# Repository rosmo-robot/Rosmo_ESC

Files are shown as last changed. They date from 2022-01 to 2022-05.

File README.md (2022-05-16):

# Rosmo ESC

Design for [Rosmo](https://rosmo.io) ESC - in M5Stack format.

[Schematic (PDF)](./Rosmo_ESC.pdf)

Top:
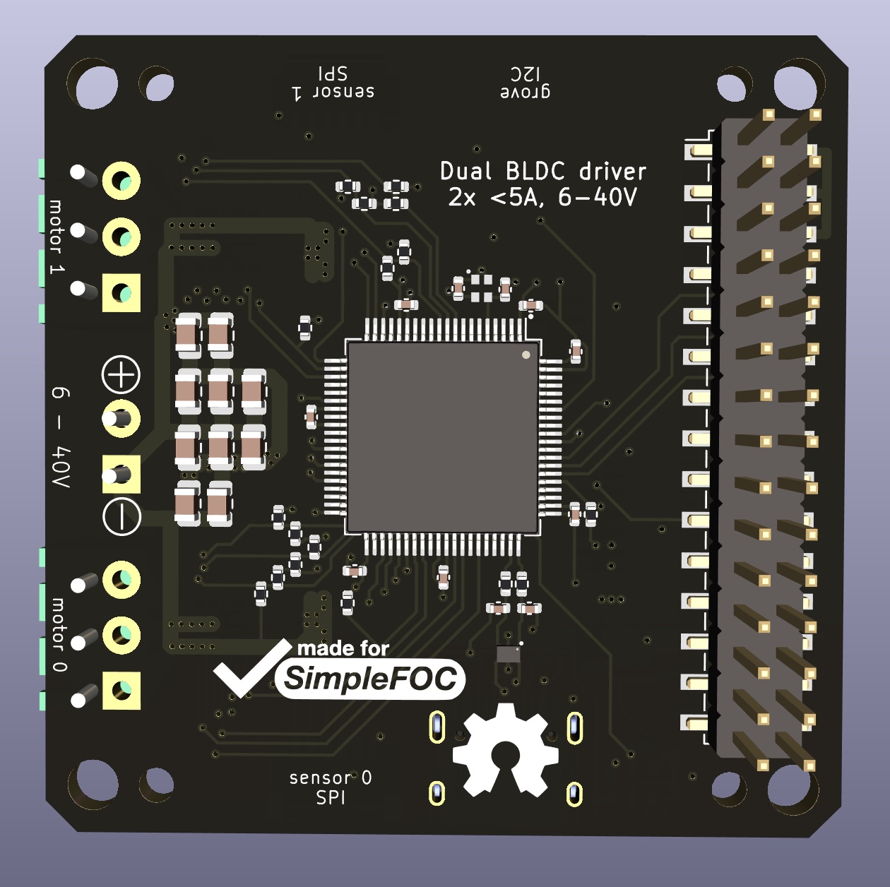
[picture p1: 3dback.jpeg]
3d render bottom 3D render of back

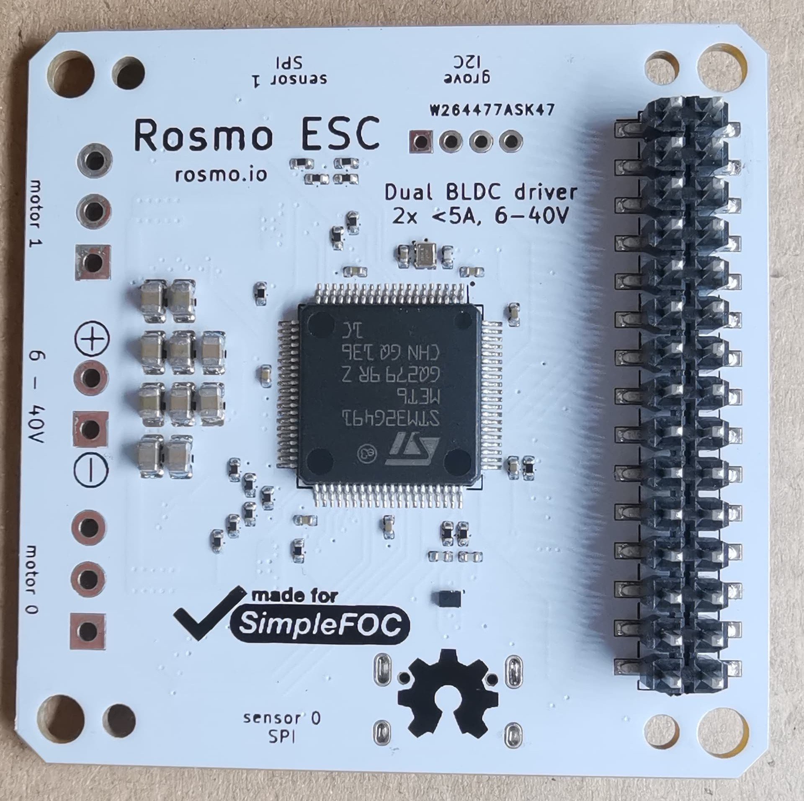
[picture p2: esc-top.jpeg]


Bottom:
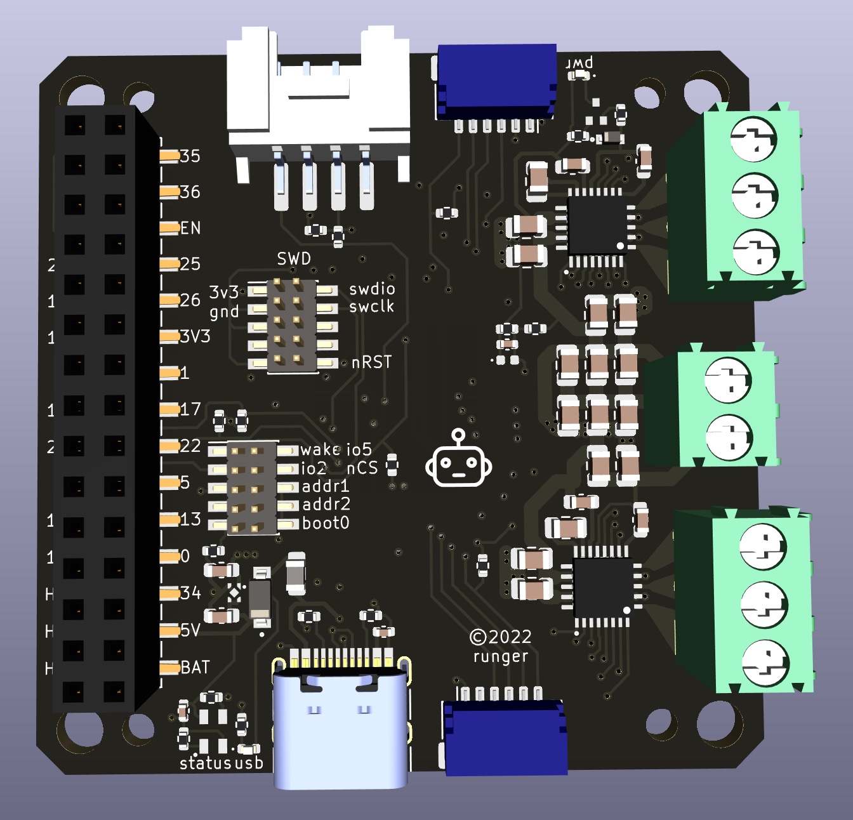
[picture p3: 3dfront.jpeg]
3d render top 3D render of top

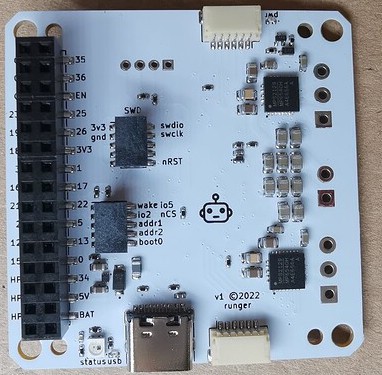
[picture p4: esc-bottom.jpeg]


## Features

* Dual brushless motor ESC in M5-Stack module format
* Drives 2x 3-phase BLDC motors with up to 40V and 5A (cooling needed - to be tested)
* 2x SPI sensors supported, such as MA732, MA730, AS5048A, AS5047, etc...
* Control inputs via SPI, I2C    (and GPIO:question:)
* Grove port for I2C input/output

## Status

:warning: In development, prototype boards on order.

At the moment, schematic is complete and board has been routed. The BOM is complete but my have to change due to component availability.

**Do not use this for anything yet!**

## Pinout

Prototype pinout, based on STM32G491MET6, which is probably not the final MCU for this design, but a suitable (if maybe overpowered and therefore expensive) one that was available in the current semiconductor shortage. This MCU is 12x12mm LQFP-80, which is more than enough pins.

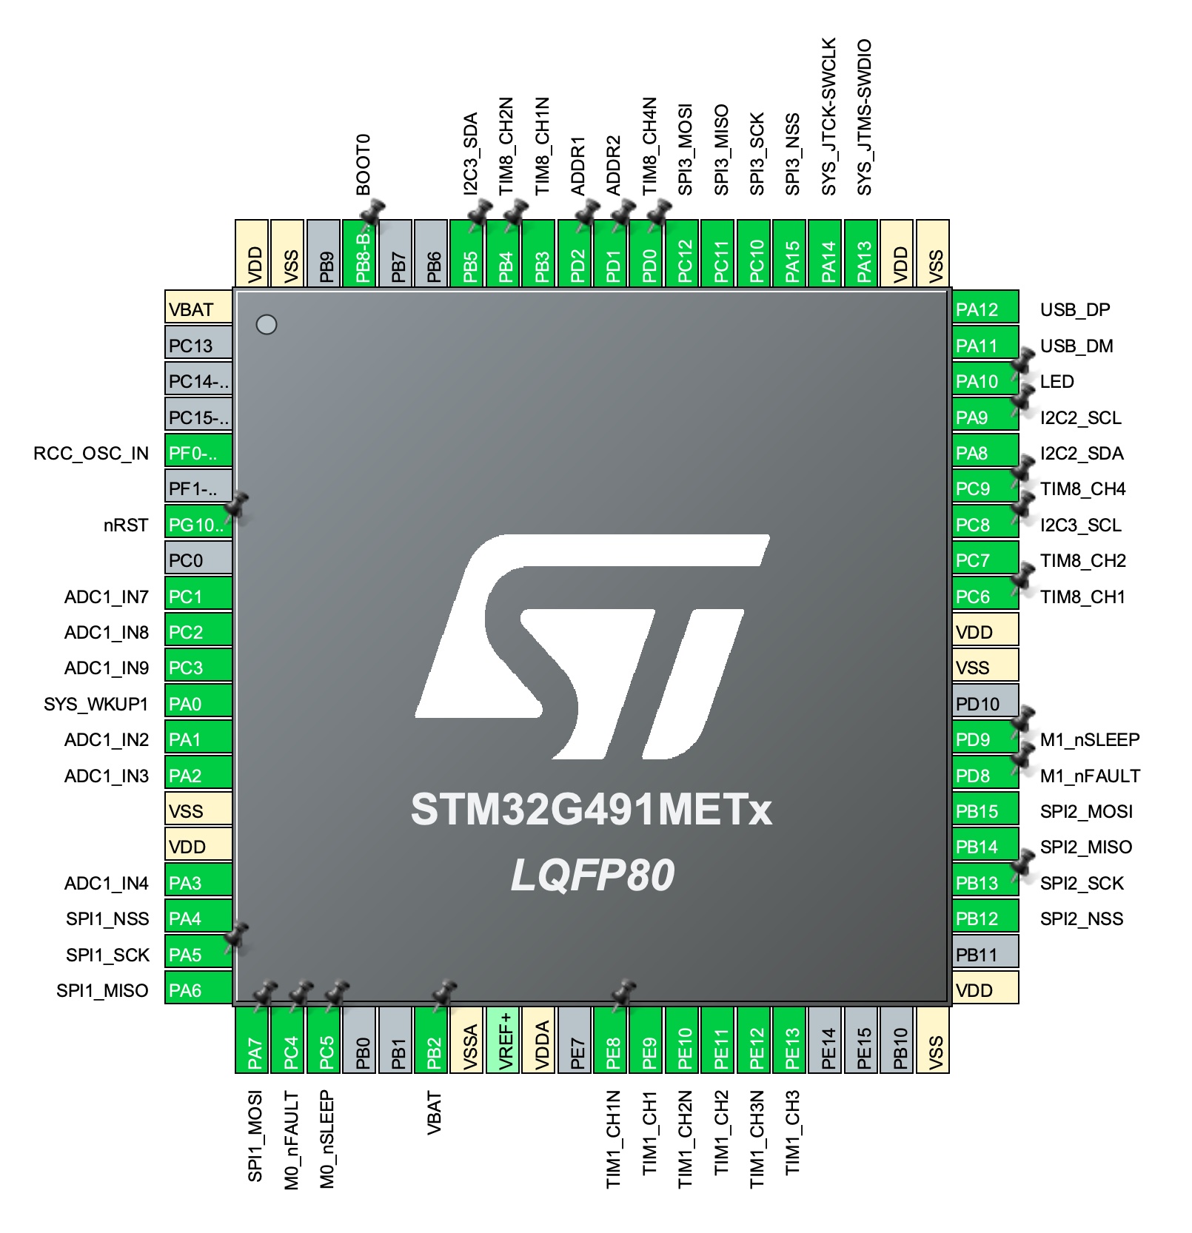
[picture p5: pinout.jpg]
pinout STM32G491MET pinout


Functionality supported by this pinout:

* 2x 3-phase BLDC motor control with 6 PWM (6 outputs on TIM1 and 6 on TIM8, in CHx/CHxN configuration)
* 2x nSLEEP outputs (GPIO)
* 2x nFAULT inputs (interrupt GPIO)
* 2x 3-phase low-side current sensing (6 single-ended inputs on ADC1)
* 1x battery voltage monitor (1 single-ended input on ADC2)
* 3x SPI w/ hardware NSS pin (2 sensor ports + M5 stack SPI pins)
* 2x I2C (grove port + M5 stack SPI)
* USB FS connected to USB-C port (should allow serial monitor function and DFU firmware flashing)
* WAKE input (M5 GPIO connected to system wake 1, so M5 ESP32 can wake STM32 from sleep)
* SWD debug pins connected to standard ARM-10 debug header
* LED pin connected to status LED (or NeoPixel LED)
* BOOT0, nRST, OSC_IN - STM32 system pins

## Dependencies

The design uses various custom symbols and footprints. They should load from the project-internal cache when you open the project. If they do not, you can find [a kicad library](https://github.com/runger1101001/kicad-lib-runger) here which contains all the symbols/footprints used, among others.

Uses KiCad 6.

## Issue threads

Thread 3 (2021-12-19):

Check clearance between screw terminals & M5 core

samuk, 2021-12-19:
We should check that the screw terminals have enough clearance when the M5 header is in place, stacked below an M5core or [Open Core ESP32](https://oshwlab.com/Rosmo/m5-proto)

runger1101001, 2021-12-19:
My plan is to use "pluggable terminal blocks" like the ODrive M5 module. I like that idea.

Normal terminal blocks won't work because the screws would not be accessible. And other connectors are either expensive, too bespoke, require crimping, etc, etc... the pluggable terminal blocks combine the ease of use and ubiquity of screw-connections with the "front access" only type of profile we need.

The pic here illustrates it nicely:
http://free-electronic.com/product/pluggable-terminal-block-2-pin/

So I have to find the ones we'll use (Amphenol I think, they're cheap) and I can send you the dimensions.

samuk, 2021-12-28:
Resolved

Closed 2021-12-28.

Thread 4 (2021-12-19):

Did you route the current outputs to mcu opamp capable pins?

samuk, 2021-12-19:
I noted you implemented the current sensors on each axis.

Did you route the current outputs to mcu opamp capable pins?

From Twitter: https://twitter.com/uuLipe/status/1472671409084243969

runger1101001, 2021-12-19:
Hmmm.. no I didn't pay attention to it. The driver has current sense amps built-in, so the signal is already amplified and in the right range for the ADC via the external resistors (if my calculations are correct!). What would the op-amps be used for?

uLipe, 2021-12-19:
Thanks for highlight my comment on twitter.

Sounds fair enough to me, I didn't noted the built-in amplification block on the driver.

samuk, 2021-12-19:
No worries, thanks for your interest. Would you be interested in testing the boards if we get a batch made?

uLipe, 2021-12-20:
@samuk , for sure, I also have m5 stack esp32 modules here and it would be great to write an initial microROS network using these modules being an initial skeleton of an mobile robot.

Closed 2021-12-19.

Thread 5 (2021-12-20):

Repository for the module firmware.

uLipe, 2021-12-20:
I think since the general idea of the hardware is up, the repository for the firmware as well the design discussions would be started.

I see this module as one of most exciting microROS over serial use cases, hot-pluggable to other microROS instances.

samuk, 2021-12-20:
Absolutely! There are a few notes in the [Rosmo doc](https://cloud.transition-space.org/apps/onlyoffice/s/KyTnsYjs4GRkXjZ), but worth discussing further.

Useful background is to know that @runger1101001 is the author of [I2C commander](https://github.com/simplefoc/Arduino-FOC-drivers/tree/master/src/comms/i2c#controller-device-brain-mcu). The ESC board will run this.

Beyond that I think it may fall into three phases;

1) A very simple [Bluetooth car](https://github.com/Yapele/Android-phone-accelerometer-controlled-Remote-Car) & I2C-commander to control to test the board(s) and bring the robot alive

2) Development of a block, or set of blocks for [Ottodiy](https://github.com/OttoDIY/blockly)which communicate using I2C-commander. I think we can probably do this in the medium term with our current capacity. Ottodiy has expressed some interest in this.

3) The uRos work. This is less clear at this point. It might involve developing this [diffdrive code](https://github.com/rosmo-robot/Rosmo_ROS2_Diffdrive) to have similar functionality to I2C-commander-master. It may make sense to use the ROS2 stack of https://nanosaur.ai/ as they seem open to collaboration, and it would save reinventing the wheel there. There is also interesting work happening in the #stackchan community around uROS, so we'll keep an eye on that. We need more people to get involved to make the uROS/2 work a reality.

runger1101001, 2021-12-20:
In terms of the firmware, we have to separate the different parts:

- the "module firmware" will target the STM32G4 MCU on the driver module. It will be expected to have a clean outward API towards the M5-stack's core MCU, probably via I2C. Th expectation is that the normal user will change this firmware rarely, if ever (so the final module may not have the USB port, to be discussed). This firmware will run SimpleFOC, which is an Arduino library. I see that µROS supports some Arduino hardware (though none with STM32G4 at the moment) - so I'm not sure how easy it is to marry these two things.
- the M5 core firmware, which talks to the motor drivers and handles all the higher lauer stuff. ESP32 is supported by µROS, and this is where I would see the freeRTOS based layer coming into play.
- the application software like blocky or a remote control app, which run on hardware external to the robot

For my part I would begin by creating a module firmware repo as the ticket suggests, based on Arduino framework, SimpleFOC and a fairly simple control layer, similar to the many commonly available I2C motor shields.

samuk, 2021-12-20:
I think we agree that the "module firmware" on the ESC driver board can always remain Arduino?

In an Otto/Blockly use case, the 'Brain ESP32' would run Arduino & I2C-Commander-Master and speak over I2C to the ESC device.

In a uROS use case the 'brain ESP32' may run Arduino (or it may be possible to port I2c-commander-master to FreeRTOS), it speaks to the ESC driver board over I2C. The 'brain ESP32' is also communicating with a Jetson/Pi/Coral over Wifi or Ethernet for the higher level ROS2 stuff.

uLipe, 2021-12-20:
I would like to add some points from the optics I have been seen when working with robots as a distributed system.

- Treat them as an isolate subsystem is great, implementing the firmware separately of the ESC on the foc module, and basic robotics stuff ( high level controllers + kinematics server) in the ESP32 sound really nice and reinforces the principle of single responsibility.

- I think the SRP design would be even greater if the modules foc, esp32 and other devices like future sensors could take advantage of same interface, allowing them to be plug-in-play, and visible across other subsystems in a form of topics.

- And here is where microROS comes into play, it would be possible to model the foc modules as abstract boxes that control motors and expose them in a format of topics, publishing commands and parameters and subscribe for their state. Same for the esp32, by modelling it as an robot brain with relevant topics.

- The microROS in their latest design support custom transports ( over UART, thus I2c), and more recently the embeddedRTPS making any microROS instance to be discoverable direclty from a full ROS2 system ( on a PC or SBC), the integration and expansion of this robot system would be smooth, since model it in abstract way, let micro ROS handle the distributed process and deal with subsystem specific role, brain, foc, imu, etc.

Would be interested in a rough draft of this design, I can spend some time on it and share with you.

Just to remember, microROS is compatible with both Arduino, and esp-idf, also it is supported from Nuttx and Zephyr which recently is being supported officially by espressif as platforms.

samuk, 2021-12-20:
`Would be interested in a rough draft of this design"`

Yes! That sounds interesting to me at least. @runger1101001 ?

As an aside, the guys at https://www.luos.io/ were quite interested in the Rosmo concept and might be interested in using the platform as a demo of Luos. Not sure how much time they actually have, or if that's just a further distraction for us in an already complex project.

runger1101001, 2021-12-20:
Yes, I would be very interested! I have to quickly add though that due to my lack of knowledge on µROS and time constraints I would support but not lead that development effort.

Regarding luos, that's also an interesting project! I'm discovering so many interesting things thanks to you, sam!

I will (as so often, sorry!) add a concern to the equation: when doing this distributed robotics/control stuff, and also when dealing with something like luos, you have to look at the real-time requirements of the components and put everything in the right place, or it just won't work.
What do I mean? For example, the FOC control of the motors is highly real-time, sub-millisecond. To run either the FOC-loop or the move-loop remotely from the PWM generating MCU is not feasible.
The next level, motion control, i.e. coordinating 2 or more motors to achieve a desired trajectory for a robot - it may be possible to run that on a remote MCU. It will be a tradeoff - comms latency will cause less responsive control and/or inaccuracy depending on the control method. Same goes for detecting and avoiding obstacles.
Higher levels like mapping and navigation are less real-time and can clearly be more easily distributed.

So despite the promise of their marketing, using a system like luos still requires a careful design of the overall architecture and what happens where, at least for a robotics system.

uLipe, 2021-12-21:
@runger1101001 that is true and I agree with you all concerns, when I worked in robotics company years ago, mostly of our final solution was a in-house engineering because at end of day the real-time requirements for having a multiple joint with high of DoF at the precise point are the main target to be achieved, so split high-rate control loops to run into bare-metal microcontollers to deal with servo controller.

At higher layer, and on the top of and ethercat bus, an single-board computer running realtime capable Linux dealt with waypoints and motion-planning + kinematics server in single ms timestep, and was responsible to generate all joints commands (position, velocity, torque).
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
uLipe, 2022-01-03:
Yes, I thinks both can coexist, the point of openning the FoC states for the host is to provide a huge advancement to the ESCs out there, which is the flexibillity of control the commands and states which the only ESC that provides that is Odrive, which would be a pain to build from source.

uLipe, 2022-01-10:
@samuk , @runger1101001 , should I start to port the I2C commander as a esp-idf component?

samuk, 2022-01-10:
@uLipe I'm excited at the prospect. The principle sounds good. I defer to @runger1101001 on the timing question.

runger1101001, 2022-01-10:
Hey, if you want to start, I definately don't want to stop you!!

I am planning some refactoring of the I2CCommander, but this will be mostly on the receiving side. In the longer term future I would like to add SPICommander and CANCommander, using the same registers, and might refactor a little more at that point.

The I2C master is really very simple, you could port what is there with not much effort. The important part is really only the registers header file, which will give you the list of registers (commands) supported.
The rest of the I2CMaster is just send some bytes receive some bytes code, and could be solved in many ways.
Its important to carefully read/write always the right amount of bytes, or the I2C bus can become stuck.

A feature worth supporting is the "report" feature, which allows the master to define a set of registers as a "report", and then read all the registers with one command. That saves a lot of protocol overhead if you're always reading the same set of values, a common use case I would expect.

samuk, 2022-01-24:
@uLipe do you think you need any further info? Or would this be enough to get started?

uLipe, 2022-01-25:
Hello @samuk , @runger1101001 , sorry for being away these days, I got the flu.

I think from my side we have now sufficient information to start building firmware, said this would you folks think I can create the firmware repository for the motor controller?

Since its responsibillity is well defined, it is also simple to prorotype some circuits while the boards get ready.

If you give me the go, I will proceed creating the firmware repo, onde point, ArduinoFoC was engineered with Arduino in mind, so the motion controllers would be developed using the Arduino (Platformio?) ecosystem right?

uLipe, 2022-01-25:
Before I forget, have you chose a particular BLDC motor plus encoder? ArduinoFoC does not have the sensorless FoC (which I personally think is only usable in aerial robotics), se we need to define also the rotor position sensor. Of course I would always prefer an opto encoder with quadrature outputs.  Because SPI / I2C encoders are very slow to process in high speed scenarios or high velocity rate variation.

samuk, 2022-01-25:
@uLipe sorry to hear you've been ill. Welcome back.

Feel free to go ahead and create a repo. Yes SimpleFOC is an Arduino program. The I2C commander linked above will be the interface to it.

We're going to use these [magnetic encoders](https://github.com/rosmo-robot/Magnetic_Encoders/tree/master/Encoder_SPI#readme) that @runger1101001 has developed. As no one was selling them with SPI cabling/sockets he's just getting ready to produce & sell them on his Tindie page.

runger1101001, 2022-01-26:
Hey, when we're talking about the module firmware here, we're talking the ESP32 code... so the business of porting I2CCommanderMaster and doing the ROS integration...
For the ESC's STM32 firmware, I will make a repo, I have most of the code I need for that together already.

runger1101001, 2022-01-26:
And note there is no rush, the ESC boards won't be here until end of Feb, due to Chinese New Years.

uLipe, 2022-01-26:
@runger1101001 , thanks for clarification, I misunderstood the question.

That is said, I'm focusing on esp32 side, hopefully I have an m5stack core in my hands so I can consider they form factor to bring-up the component.

By moving with the IDF approach, the module firmware would be a component compatible to the ESP-IDF and inside it it would be possible to provide some application through an example folder, which is compliant with IDF component structure.

Other thing I would like to highlight is uROS supports WIFI interface, which I see very interesing cases of Rosmo robot fleets :)

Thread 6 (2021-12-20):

Support for CAN-Bus

uLipe, 2021-12-20:
I see the module uses an overpowered stm32 microcontroller.

Since this is true, what about select a cheaper one like stm32g431, which has CAN and leave this possiblity besides the traditional serial buses, making this module networkable :)

samuk, 2021-12-20:
@runger1101001 may have comment here.

Don't forget the existing modules which can be plugged in to add functionality. https://shop.m5stack.com/products/commu-module?variant=16804786896986

runger1101001, 2021-12-20:
Hey, this is a very good comment.

Yes, the MCU is somewhat overpowered. And it is expensive. And it is big. But, we were trying to create a prototype quickly, and it was available right now (only 20pieces) and so I ordered it and have it.

The final design should be optimised to use a different MCU if possible.

But, on the other hand, I would also make the following points:

- having more pins available than strictly necessary greatly eases both enabling the functionality (for example I think I could still activate CAN-bus, pins are available I think) and the routing, since pins can be moved around the MCU to find the best spot
- so a smaller 80 or 100 pin MCU would be appropriate
- LQFP is big, but in the end I routed it with only 0.6/0.3 vias - switching to a smaller MCU with 80 or 100 pins would mean BGA, and probably microvias, maybe even 6 layers, and ultimately a more expensive board
- driving 2 motors with 6-pwm and current sensing requires quite a bit of MCU power, so a G4 is actually not too overpowered

In terms of functionality:

- adding CAN would definately be possible, but unlike the grove I2C port which comes at the price of the connector + 2 pull-up resistors, a CAN bus would need a transceiver IC, 5V power, choke/filter, termination selection, etc... and I can tell you right now the small size CAN transceivers are all out of stock; since the CAN-bus can be added using existing M5-stack modules, we made the design decision to leave it off
- personally, I would add a buck converter to the design. Since we already have high voltage coming in, we could power the M5-stack from the ESC board, and save the user having to buy a separate base module for this
- the current design is "networkable" via I2C bus. We could easily add SPI to this, the design already connects to the M5 stack SPI bus, we would only need to add some headers to make the CS-pins selectable to enable multiple modules via SPI.
- CAN only makes sense if the modules are far apart. I'm not speaking out against CAN here, I think it is ultimately better than I2C, but also more expensive. In the context of M5-Stack, doesn't it make more sense to have stacks of drivers, locally connected via the M5-header to a M5 Core, which talks to them via I2C. The M5 cores have WLAN, and can communicate with each other that way. I think this approach is probably more what M5-users would expect?

uLipe, 2021-12-20:
All the comments above are reasonable, my point is to see the CAN-Bus as an additional, not a replacement from I2C or SPI.

The main point of CAN is the possibility to have an distributed network with bitrate higher than I2C, would be an option to route the CAN-TX + RX pins to solder pads and advanced users could stack an transceiver board if they have, I think would have some value to make this board "hackable".

The SPI option is great since it would allow to plug the m5 wiznet modules, allowing to make a true networkable, high-speed and maybe a microROS native motion module.

runger1101001, 2021-12-20:
Ok, I checked the pins, and the CAN is currently blocked by BOOT0, which I haven't routed out anywhere though. I'm unsure if it is needed - normally not for either DFU or SWD programming... perhaps a question for the STM forums to be sure, I can't 100% say from the datasheet. There are also BOOT-bits that can be set via the flags, so that could be another option.

Otherwise if BOOT0 is needed it could be used in conjunction with a CAN transceiver that has an EN-pin. Then we could disable CAN until boot-up is completed, and the BOOT0 pin would not be in the way. I'll try to see what can be done here.

The pins for a 2-pin (no flow control) USART connection are available though, so I will route those out still, and then we will have the option of asynchronous serial or RS485 as well.

samuk, 2022-01-07:
I think this is a wontfix for now so closing.

Closed 2022-01-07.

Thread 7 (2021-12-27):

Rosmo power supply concept?

runger1101001, 2021-12-27:
The power supply concept for Rosmo needs more attention.

The motors chosen are for 12V. They will run with less, but since they have quite high resistance the current, and hence the torque will be low.
m5stack power concept is very unclear to me. I can't find good documentation. [The schematic I can find ](https://github.com/m5stack/M5-Schematic/blob/master/Core/Basic/M5-Core-Schematic(20171206).pdf)has part of the power circuitry labeled "Speaker" :-( .

The general idea with m5stack seems to be that the core provides power to the rest, it has a 5V buck/boost converter with battery charging and 3.3V rails. It has a HPWR rail on the M5 header but it doesn't seem to connect to the core. The buck/boost converter is powered by the battery and the 5V_USB rail, and I assume will manage switching between these.

Currently the Rosmo ESCs 5V_USB rail connects into the 5V rail of the M5 header via a protective diode, so powering the core *should* would providing the Buck/Boost module doesn't mind this configuration (having its output back-powered).

An alternative could be to connect the 5V_USB to the VBAT on the m5 header, i.e. pretending to be a battery. Not sure if the buck/boost module will like that one either.

In any case the input to the ESC board should be at least 6V. The current design is for 4x1.5V battery, so this is just enough, but only when they're more or less charged up. Once they become empty the voltage would drop below 6V which is not ideal.

Note that the m5 core's battery charging is for 4.2V lipos or Lions, not for NiMH batteries in 4S. So I currently don't see how the m5stack itself is powered. The little battery in the base of the core module? – but the 3D design doesn't account for that...

Some ideas:

- get rid of the NiMH batteries in favour of a beefy 1S battery [like this](https://www.spystore.at/3-7v-2000mah-wiederaufladbarer-lithium-akku-e126849.htm) for example. This would get charged by the m5 core when plugged into USB, and could power everything for a little while. You'd need a boost converter board to boost it up to 12V for the ESC board input.
- use a 3S battery, something [like this](https://batteryzone.de/products/11-1v-2500mah-3s-hochleistungs-lithium-polymer-akku-fur-ferngesteuertes-auto-flugzeug-hubschrauber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). There are other shapes and sizes. The 11.1V will be fine for the ESC and motor. Use a buck converter module to produce the 5V to power the m5 stack.
- use the NiMH battery pack, together with a boost module to get 12V and a buck/boost module to get stable 5V.
- I'm sure there is a M5stack LiPo Power-Base? Integrate that into the design and use a 3S battery?
- Add a 5V buck converter to the ESC board. Then the ESC board can power the m5 stack directly from its 6V-40V input.
- Add both a 5V buck converter and 3.3V regulator to the ESC board: then the ESC is fully self-contained (i.e. could be used without the core module), and can power the m5stack if attached to it.

runger1101001, 2021-12-27:
Hmmm... this schematic for Core2 is a bit better: https://m5stack.oss-cn-shenzhen.aliyuncs.com/resource/docs/schematic/Core/CORE2_V1.0_SCH.pdf

It shows clearly that HPWR isn't connected to the core. The other issues around VBAT 5V_BUS are the same.

samuk, 2021-12-27:
Just to clarify my current thinking is to use 3x 3.2v lifepo4 cells: https://m.aliexpress.com/item/1005002959027031.html

They share the same physical dimensions as Aa batteries.

runger1101001, 2021-12-28:
Ok, I will try to find space for it! I'm more optimistic about that than the CAN bus TBH. I can't really fit another port around the outside.

samuk, 2021-12-28:
On board canbus would be nice, but would also add cost. Don't we get similar functionality from plugging in a M5comm module for those use cases that need it?

runger1101001, 2022-01-07:
Ok, I've spent about 10h on the buck converter and I'm changing my mind on this:

- due to chip shortage none of the designs I've made before can be produced at the moment
- designing a new one based on available chips is a bit of work, and carries some risk - risk that it won't be right and messes up the rest of the board. Then we'd have to manually desolder stuff to be able to use the prototypes, I'd prefer to avoid that, really
- having it on a board with MCU and all the other stuff is also an expensive way to prototype the buck converter, which only needs a few components itself

So the new plan to is to release the board as it is, adding only a 3.3V regulator so it is self-sufficient when plugged into USB.
For the prototyping, we can use one of the many cheap and tiny buck regulator modules ("BECs") that are available on AliExpress or eBay. There will be space for it in the Rosmo body.
Then I can design a new buck converter for the Rosmo board v2, prototyping it separately, and then integrating it into the v2 design. At that point we'll also have a clearer idea what we want - maybe with battery charging? Or maybe more basic, just for the ESC board and seperating it from the whole complexity of the m5 power?

samuk, 2022-01-07:
Great, thanks for investigating! This sounds like a sensible way forward. I'm happy to spend a bit of time looking at existing open-source buck designs to see what we could make in the current chip situation.

Closing this, for now, we can create a new ticket when we want to look at this again.

runger1101001, 2022-01-07:
No, the regulator is still missing and the m5 header... I'll export it again today if I can, but certainly before I order it.

Closed 2022-01-07.

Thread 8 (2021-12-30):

Create step file of board to enable case design

samuk, 2021-12-30:
@runger1101001 when you have time could you export a .step file of the ESC please so we can design the 3D print case to fit.

Ref
https://github.com/rosmo-robot/Rosmo_3D/issues/2

runger1101001, 2022-01-03:
[Rosmo_ESC.step.zip](https://github.com/rosmo-robot/Rosmo_ESC/files/7804330/Rosmo_ESC.step.zip)

The STEP export only includes the ports and a few components, all the other components don't get exported... but this should give the outer dimensions, and the since the ports are on there... note the terminal blocks are not the right ones...

samuk, 2022-01-03:
Nice one, thanks. Should be OK for the case design.

Closed 2022-01-03.

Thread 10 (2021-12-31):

Specify dimensions of encoder board

samuk, 2021-12-31:
As discussed it makes sense to develop a small encoder board so that users can plug and play the encoders. It would be good if this encoder could be used in a variety of motors.

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

I suggest we stick broadly to the above dimensions, whilst noting that the [BGM220](http://www.dys.hk/product/BGM2208-70.html) has 16mm spacing for the screw holes, so two 'notches' in the left and right of the above dimensions would give compatibility?

There would be a 7mm wide, side entry [JST SHR-06-VS ](https://www.jst-mfg.com/product/detail_e.php?series=231) without flange specified for soldering to the SPI side. This would be positioned 'in reverse' with the cabling going over the encoder chip so that it could be used in a [2205](https://ae01.alicdn.com/kf/H5db205d3acb24197b1f93c58d5f370b9e.jpg)

runger1101001, 2022-01-03:
Here a picture and 3D render:

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

This is the pinout:

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

These are the dimensions:

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

runger1101001, 2022-01-03:
If we can work with these for the prototype, then I have bunch here. I can provide AS5048As or TLE5012Bs in this shape.

If we want a different shape, we'd have to have some made :-)

samuk, 2022-01-03:
Great! nice one..

samuk, 2022-05-07:
These are now available here: https://www.tindie.com/products/smallrobots/as5048a-encoder-board-for-robots-motor-control/

Closed 2022-01-03.

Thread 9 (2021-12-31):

Export BOM

samuk, 2021-12-31:
It would be good to get a BOM, even if provisional and subject to change. It will enable us to get some ballpark production quotes.

runger1101001, 2022-01-03:
[Rosmo_ESC.csv](https://github.com/rosmo-robot/Rosmo_ESC/files/7804442/Rosmo_ESC.csv)

This is the current BOM.
This is the more or less finished board, but without the buck converter... I'm still playing with the design for that.

runger1101001, 2022-01-03:
I still need the part numbers for the M5 bus connector, top and bottom...

samuk, 2022-01-03:
Does this help? https://shop.m5stack.com/products/2x15-pin-headers-socket I can ask them on Twitter..

samuk, 2022-01-03:
Looks like you could specify the 3mm Samtec one? https://community.m5stack.com/topic/1980/pin-header-and-sockets-part-numbers

samuk, 2022-01-07:
In light of https://github.com/rosmo-robot/Rosmo_ESC/issues/7#issuecomment-1007344152 I think the BOM is final-v1 at this point?

runger1101001, 2022-01-09:
Hmmm... the Samtec one is 1.27mm pitch but the M5 bus is 2.54mm pitch. So that's not the right one. I'm beginning to to like this m5 stack so much, using custom connectors is just a pain.
If the grove port turns out to be a problem to procure I will change it to be a Stemma/QT I2C port instead.

I'm just going to assume standard 2.54 pitch SMD headers will work, the footprint looks like they will. We can ignore the alignment holes, I think, 30 solder joints should be strong enough for a few plug in/out cycles.

runger1101001, 2022-01-09:
Ok, this is more of an issue than I anticipated. Their custom connectors are also lower profile than standard ones. The lowest profile ones I've found so far, at mouser, have 3.05 or 3.6mm pins, but the standoffs are also taller than the m5 stack ones.
So you would end up with about 7.5-8mm distance between the board and the end of the pins.

But worse than that, these headers cost EUR5,50 each (!).

The smallest reasonably priced header will come to EUR0.70, but result in a board to pin distance of about 10mm.

I'll see if I can find anything else, at digikey for example... what a pain.

samuk, 2022-01-09:
If all else fails we could just buy the official one and have them shipped to whoever is doing the boards? https://shop.m5stack.com/products/2x15-pin-headers-socket

runger1101001, 2022-01-09:
I've included headers that should work - both sides for about $6, ugh. We can account for the difference in height in the ESCs shell, it will be a little taller module than necessary, but that could be a good thing anyway to get the heat out...

samuk, 2022-01-09:
Did you see these @75cents/ pc? https://shop.m5stack.com/products/2x15-pin-headers-socket

runger1101001, 2022-01-09:
I did look at that, but then I'd have to order them from m5stack, pay shipping+tax, send them back to china, pay shipping+tax, and by that time they wouldn't be any cheaper. And it would take an extra 1-2 weeks. Unfortunately, the forum already said PCBWay won't order from m5stack. And probably they wouldn't accept them for assembly anyway, since they're not on tape&reel.

Plus I don't really trust what I'd be getting. The picture says 10x set, the title says "4 pieces" and the description says "Includes 1xheader 1xsocket"...

I've put in the order for quotation... its a little more than I anticipated, they won't give the $30 assembly deal for some reason, prob. because it has 102 components or something. So for 10 boards + assembly it will come to $300 or so + the components, which still have to be quoted, but I'm guessing will come in at another $400 (counting the drivers and MCUs which I already have at around $20).

So we're looking at somewhere around $70/board for a quantity of 10. Looking at the prices for making 50 pieces, it looks like the price would  be more like $10/board + components, so $30-$40/board.

runger1101001, 2022-01-09:
Yeah, its the component count that's driving up the price... but if I lower the number to 5 pieces to get the $30 deal, assembly is cheaper, but the PCBs cost is the same for 5 or 10 pieces... so the final cost is still around $30 per board. :-(
Still, we could save a bit by only producing 5, since we'll only need half the number of components.

samuk, 2022-01-09:
Shall we go for 5X? To start with? Split the cost between us and try and sell the 3x spare boards for $30 + P&P?

runger1101001, 2022-01-10:
Feedback from Fab so far: grove connector and m5 female header are unavailable...

I'll look for an alternative header, the female ones were not so hard to find.
I would suggest swapping out the grove connector for a JST 4-pin Stemma/QT style one? Or replacing it with just solder-points for a through-hole model?

runger1101001, 2022-01-10:
You mean leave the SMD footprint, and just leave it out? Sure, I could do that too. But there are also through-hole grove connectors, they'd be easier to solder.

samuk, 2022-01-10:
Yes, I understand your previous comment now, I'd assumed they were already through-hole. Let's do through-hole ones.

samuk, 2022-01-11:
https://store.open-electronics.org/2x15-Pin-Headers-Socket-2,54mm-Male-Connector-5330-M5CONN2X15M

runger1101001, 2022-01-11:
Those certainly look a lot cheaper!

But I have to stress that it isn't so easy as finding a web-link just anywhere. That doesn't look like a very well established store (don't know, just going by the website), and often fabs won't just order from anywhere - when they accept a order for assembly they take on responsibility for being able to source the parts incl. shipping, duties, etc... at the quoted price, have to meet the promised deadlines (in theory), and so won't take any risks... and that store is in Italy, so by the time those headers are at the fab in china you have add at least EUR30 in shipping, meaning for 10 pieces they're no cheaper than the ones we have.

And from the product page, it isn't clear it comes on a tape&reel with a pick&place compatible "pickup". The pick&place machines can't just grab a bare header, they need a kind of plastic cap on there.
If they don't have that the assembly has a manual placement step and things get more expensive that way.

Unfortunately you can't just send them a bag of components and say "assemble this". Its a bit more complicated.

runger1101001, 2022-01-11:
(I'm not trying to be negative, I'm just trying to explain why its not so easy. I strongly agree that a cheaper solution would be better, and that's something we should improve in V2).

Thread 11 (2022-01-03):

Step/ Dir?

samuk, 2022-01-03:
I spotted that Odrive has Step/Dir https://docs.odriverobotics.com/step-direction

I know it's kind of crappy, but might be nice to support for 3Dprinters/CNC etc if not much work.

I read this on the [software ](https://community.simplefoc.com/t/simplefoc-and-linuxcnc/556/12)

runger1101001, 2022-01-03:
We're running quite low on pins, but in particular board-space too... I'm just working on it, so I'll look into it.
Some options:
- we could support it using the m5header, but not give it its own port
- we could support it in software, i.e. via the SPI, I2C, UART or CAN inputs, and handle the step/dir impulses on the ESP32.
- we could drop support for something else, and add 2 x step-dir inputs connected to timer pins

My feeling is to leave this for the prototype version, and come back to it at a later time. Our principle goal is to create a solution for robots and not 3D printers. 3D printer users would prefer a different board, with support for 3 axes, inputs for end-stops, bed heating & fan outputs, etc...

samuk, 2022-01-03:
My feeling is to leave this for the prototype version, and come back to it at a later time.

Great. Say no more!

Closed 2022-01-03.

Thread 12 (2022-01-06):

STM32G491MET6 availability

samuk, 2022-01-06:
So when @runger1101001 designed the board the parts were available. Unfortunately, that's no longer the case: https://octopart.com/stm32g491met6-stmicroelectronics-114199453#PriceAndStock

Farnell [claim some are coming in](https://uk.farnell.com/stmicroelectronics/stm32g491met6/mcu-32bit-170mhz-lqfp-80/dp/3648860) and hopefully they will, but other suppliers are showing a 6-12month lead time.

@uLipe floated the idea of an ESP32 version? I understand that you may not want to start from scratch & It may just be a case of waiting for parts to be available.

uLipe, 2022-01-07:
What would be the complexity to replace the stm32 to an ESP32 wrover -B module?

Please consider the ESP32 regardless the version has less GPIO than this STM32.

Otherwise it offers almost same peripherals or features.

runger1101001, 2022-01-07:
:-) the MCU shortage was anticipated. Indeed, the choice of MCU is not optimal, and is due to the shortage. I bought 20 pieces while they were one of the very few STM32s available at mouser, and the whole idea was to design the prototype for this MCU, because I have it on hand!
I can do kitted assembly at PCBWay to produce the prototype boards, and then there will be something to test, play with and make some initial videos of. :-)
Once this chip shortage situation improves, which looks to happen sometime during this year, we can produce more boards. And in the meantime we can design v2, based on the experience with the prototype, and targeting the right MCU that we want.
And the MCU we want is a cheaper, smaller STM32 in my opinion. The ESP32 is a great chip, but less well suited to motor control than the STM32s. It's ADCs are not as good, and the timers are less flexible. But the main problem is simply the number of pins. Even if you could use all the pins it would not be enough for 2 x motor + current sensing + 3 SPI buses + 2 x I2C, etc.... and the fact that you effectively can't use 6 of the pins because they're connected to the flash RAM means this chip is well suited to IoT use cases that use its built in WiFi, but not so much to this kind of task.

samuk, 2022-01-07:
Thanks, that clarifies the situation well I think. I have a few people who have expressed interest in the boards.

How would you plan to use the STM32 you have? 5pc run initially to test, then a v2.

Or is it worth doing a 10pc run, keeping 10x STM32 in reserve?

runger1101001, 2022-01-07:
I would produce the max number possible under the inexpensive "prototyping deals" offered by the manufacturers. In my experience this is least expensive per board at low volume.
So at PCBWay, for example, this will be 10 boards, but the board has 100 components right now, and there can be other constraints like component limits which might mean they'll only make 5 or 6 boards for the low price.
I'll try to get a few quotes this WE, and order a first run.

samuk, 2022-01-07:
Great thanks, I think it would be good to get one into @uLipe's hands if possible.  I want one too Obvs :)

uLipe, 2022-01-07:
Although ESP32 does not have the same good ADC than STM32 the chip would offer other features one of them is the fact of being a true dual-core chip, where is possible to left an entire core to control the motor tasks under FoC scheme ( and even in sensorless control), also there is an option of the MCPWM which is targeted to motion control able to generate by hardware the 6-pwm signals with configurable dead-time and hardware fault detection.

The problem I see here is the true miss of pins, which is being fixed on S3 model.

I'm just highlighting this because we're developing internally an motor control kit with a motion control component around s3.

Besides S3 or ESP32, what about using texas instruments C2000?

runger1101001, 2022-01-07:
Hey, the ESP32 is a great chip, and I have used it before in motor controller designs. I love the fact it has a IO MUX so much! It really is a great chip.
But please believe me that it can't handle 2 motors in 6-PWM + current sensing + SPI buses...

SimpleFOC uses the MCPWM module to run the PWM on ESP32.

I look forward to trying out the S3, and maybe it is the right chip for the v2 design, lets see.

I have no experience of the C2000 architecture... is it well supported in Arduino? Unfortunately we don't currently support it in SimpleFOC, so one would have to write PWM and current sense drivers...

Closed 2022-01-07.

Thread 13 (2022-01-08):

Create Altium viewer?

samuk, 2022-01-08:
Would it be possible to export the ESC file from Kicad> [Altium viewer?](https://365.altium.com/files/CDB3C9AB-1C0E-4B25-A3A4-1780F1BBCA1A)

I haven't been able to navigate Kicad6 personally. It might make it easier for people to help review the board?  No worries if not, or you don't have the time to investigate.

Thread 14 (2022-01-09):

Stacking issues & 9v Battery

samuk, 2022-01-09:
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

@sathya131295 started looking at the case for the ESC. https://github.com/rosmo-robot/Rosmo_3D/issues/2

Is the intention to orientate the board as in the image above?

sathya131295, 2022-01-10:
@runger1101001

Current components placement won't be compatible with the stack.
Issues I noted,
1. the m-bus header and the other components are placed on the same side.
2. Terminal blocks' position with respect to the m-bus header is not right if we want to route the wires inside.
3. Different sized terminal blocks will interfere with M5-Core standard screw holes.

Also, try using only the 3.5mm terminal blocks, or even better 3.5mm right-angled pluggable terminal block.

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

I suggest a layout like this to match with the m5 stack.

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

samuk, 2022-01-10:
Thanks @sathya131295 could you elaborate on

"2) Terminal blocks' position with respect to the m-bus header is not right if we want to route the wires inside."

In what sense is it 'not right' don't we simply rotate the boards' stack to orientate the cabling correctly against the robot body?

runger1101001, 2022-01-10:
The terminal blocks used are the pluggable 3.5p ones, like the ODrive module. They have 7mm height. There is no 3D model for them, so the terminal blocks shown in the 3D model are not the correct ones.

The m5 headers shown in the 3D models are not the correct ones. There are no 3D models for the short male headers, and the female socket header is not quite the right height either.

The orientation seems to be normal for m5 stack - the ODrive module is the same. Because the "top" of the board connects to the m5 core, or the previous module in the stack with not much space to spare, any tall components have to go on the "bottom" of the board, facing downwards...

And thus the module has 2 x m5 headers, one male, as short as I could source it, sticking up from the top of the board, and one female socket, 7mm tall like the terminal blocks, sticking down from the bottom.

So the module is stackable, and should accept other modules top and bottom, or a core module on the top. The fact that the header spacing isn't exactly like other modules which use the proprietary headers can be accounted for by making the module's shell a little taller as needed.

Based on this description, do you still see an issue?
Should I order blank boards before assembled boards? Then we could hand-solder in the terminal blocks and some headers and try it out first? It will add 2 weeks at least to the timeline before we get the working prototypes...

runger1101001, 2022-01-10:
Regarding your other points,
> Is the intention to orientate the board as in the image above?
Yes, that looks right!

> Terminal blocks' position with respect to the m-bus header is not right if we want to route the wires inside.
I don't quite understand this. From the first picture in this post, the terminal blocks would be facing the front of the robot, that's perfect, right? Keep in mind the sensor cables come out the side though.

> Different sized terminal blocks will interfere with M5-Core standard screw holes.
The 3.5mm pluggable terminal blocks chosen are Amphenol ones, and they will not interfere with the holes. There are similar ones from TE Connectivity which should work too. They're not expensive.
Depending on how far they stick backwards from the holes users will probably also be able to choose other terminal blocks. Ones that stick out too far left and right won't work, but hey, we can't support all the world's terminal blocks ;-)

runger1101001, 2022-01-10:
Dimensions of terminal blocks used: https://www.mouser.at/datasheet/2/18/20020110-941881.pdf

samuk, 2022-01-10:
> Based on this description, do you still see an issue? Should I order blank boards before assembled boards? Then we could hand-solder in the terminal blocks and some headers and try it out first? It will add 2 weeks at least to the timeline before we get the working prototypes...

I'd say let's get them populated personally. We could de/re-solder the terminal blocks if they really don't work?

@sathya131295 apologies if I opened the case issue too soon, in retrospect I should probably have waited until we had real boards existing. Would it be better to delay any further work on https://github.com/rosmo-robot/Rosmo_3D/issues/2 until we have them? Would it be helpful if we post you a real board once they arrive?

sathya131295, 2022-01-10:
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

In the current layout, the terminal pins are on the opposite side of the header pins, which will result in an orientation like this. we will need to rotate the core 90deg. If we do that, the power button will collide with the body, and the face of Rosmo will not be symmetric.
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

The m-bus headers and terminal blocks must be adjacent to each other is what I feel.
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

runger1101001, 2022-01-10:
I see the problem now... the power button...

Some ideas: maybe it could be turned 180°? The cables would have to reach further, but it's only 5cm, and the power button would then be on the rear. What do you think?

Changing the terminal blocks to be on the side is not so easy. Current layout looks like this:

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

So the sides have the mounting holes, and considerably less space for ports. The terminal blocks would be quite close to the mounting holes, but also the drivers and power-in path with the capacitors are 35mm wide, it will be hard to fit. Not impossible, but hard.
And it's not just a matter of rotating the existing layout, since the m5 header would have to stay put, and therefore one set of ports would have to be moved... a lot of work.

And finally, what about Rosmo2, Bosmo and Cosmo (i.e. the next generation of robots)? I have the feeling that the terminal blocks opposite the m5 header, with the sensor ports to either side, is somehow a more "generally useful" configuration.

runger1101001, 2022-01-10:
> We should consider adding a physical on-off switch

Normally I would always agree to physical off switches (for safety) but at the envisioned power levels, with the motors we're planning, there really is no need. you can always just pick the robot up, and the motors will stall long before causing injury, or even pain.

> but my view is we should test things more or less as we have them now.

I would strongly encourage that. We've come a long way already with designs and "theory" and its time to put it on the road, and try it out. That there will be changes is clear, and acceptable. But otherwise I fear we might put in a lot of "empty miles" optimising things we will decide to do differently anyway once we try it out.

samuk, 2022-01-10:
> Normally I would always agree to physical off switches

I think we should do it if we can I'll have a look for something suitable. Otherwise, users are likely to leave the ESC powered for an extended duration.

I chose the LifePO4 largely because they're one of the safer lithium chemistries AFAIK.

sathya131295, 2022-01-10:
I have given some mounting holes in the Rosmo body. I feel you can use some Hex standoffs and mount the PCB in the body itself, for testing purposes. It will save on 3D printing costs too.

samuk, 2022-01-10:
Perfect, thanks @sathya131295

runger1101001, 2022-01-10:
> Otherwise, users are likely to leave the ESC powered for an extended duration.
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
samuk, 2022-01-10:
> for very little benefit since the M5 core already has switches.

The risk I see here is fire.  I'm not worried about legal liability, but rather moral.

If you're confident that leaving the ESC energised represents very little fire risk then that allays that fear somewhat. We can also say that people should remove the batteries when not in use. In the BOM I've specified what seems to be a reasonably good external USB charger. Getting the batteries in and out will be a bit of a pain, but we can revisit power again in V2.

Probably should add a switch to the Open core..

runger1101001, 2022-01-11:
> The risk I see here is fire.

LiFePO batteries are fairly fire-proof, but of course at 10A something else could catch fire. On the other hand, if the robot is burning, it's quite small for a safety switch.

As an off/on switch it makes sense, but for it to be compatible with the ESC design with dual 5A drivers it would have to handle 10A... And with all the capacitors on there the initial switch-on currents can be very high. That could be quite some sparks, it should definitely be a high quality switch, the board only has quite basic ESD protection. On the other hand the intended motors are high resistance, so currents can't rise that high anyway (until the motor melts) so you could think about using a smaller, lower powered switch. I don't know.

It's easier in some ways (and definately cheaper) to handle it in the software side, i.e. by reading a simple low voltage button or touch sensor not on the power path, and then disabling the drivers and MCU in software. The drivers are FET switches, so power is cut to the motors, and in the end the result is the VIN isn't powering anything except the pwr indication LED and the part of the drivers that remains active during disabled mode to monitor the enable pin.

But your intuition is quite correct that a switch on the power path would be safer and better. Just more difficult.

>  We can also say that people should remove the batteries when not in use.

I agree, one should definately do that in a "self built" type robot. Its not a finished device like an iPhone.

> Getting the batteries in and out will be a bit of a pain, but we can revisit power again in V2.

I will definitely design a kind of power board, but if Rosmo is to be inexpensive then I would see if we can't find a suitable inexpensive battery charger board on AliExpress. Depending on its features it may solve the on/off switch problem too.

A custom power board with reverse polarity protection, battery charging, power path management, etc will be expensive, maybe not quite as much as the dual ESC but similar.

samuk, 2022-01-11:
The Ottodiy solution is quite neat: https://store.ottodiy.com/product/booster/ maybe we should try 9v and see if it's adaquate for our needs?

runger1101001, 2022-01-11:
That is super-neat, but the product doesn't say what voltage it is, or am I blind? I'm assuming not 9V though.

How does the 650mAh compare to the 3 LiFePOs?

samuk, 2022-01-11:
Yeah 9v: https://www.amazon.co.uk/650mAh-Battery-Rechargeable-Keyboard-Microphone-White/dp/B07HYSMD51

runger1101001, 2022-01-11:
Hmm, they're 8.4V, so probably 2S LiPos. 9V just isn't a LiIon/LiPo voltage. But close enough. They'd work, methinks.

samuk, 2022-01-11:
See also: https://github.com/electronut/ElectronutLabs-snapVCC

+ something in the middle to get the 9v out

runger1101001, 2022-01-11:
Nice, a Y-cable for 9V battery tabs must be something that exists...

Really nice, I like that 9V battery emulation very much. A super-nice solution. If we could find one that has under-voltage protection it would be a pretty perfect solution!

samuk, 2022-01-11:
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

Let's just steal Otto's power system? This is the [buck](https://www.aliexpress.com/item/33041610656.html) they use.

runger1101001, 2022-01-11:
Nah, I'd combine the Otto buck with the 9V (8.4V) rechargeable you found and that's perfect! We can even make a little hole or door in the case to make it chargeable without removing it. And the power switch to disconnect it when not in use.

samuk, 2022-01-11:
Big Clive seems happy with these https://youtu.be/dR_RusM99no?t=239

So I'll update the BOM with a Znter: https://www.aliexpress.com/item/32985529438.htm

Think this thread has served it's purpose on the stacking and battery questions, so closing now.

Closed 2022-01-11.

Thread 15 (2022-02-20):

Stackable?

robottini, 2022-02-20:
Is the board stackable? Can I drive 4 motors?

runger1101001, 2022-02-20:
:-) Yes, it should be! I say _should_ because I'm waiting on the first test production, and have yet to try it out...

But the concept is to use I2C for comms, and there are 4 hardware-settable addresses, or you could set addresses in software. So the boards should stack.
In addition, they have a grove port (also I2C), so multiple stacks could be connected via cables, allowing a very large number of motors in theory.

Working against this concept is the limited space m5stack leaves for heat-sink or fan. So while I still have to try it out, I think much more than 2A will be unrealistic without a heat-sink of some kind, which will impose physical constraints on the stickability...

robottini, 2022-02-20:
thanks! I wait for a test!

Closed 2022-02-20.

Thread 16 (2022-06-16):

Make this board supported into Zephyr RTOS.

uLipe, 2022-06-16:
Although this board is intended to  receive the Rosmo ESC firmware based on SimpleFoC, I have a strong feeling that this board could gain vast popularity if it gets supported in the Zephyr Project RTOS.

Since it supports device tree, lifting its features and provide motor control bindings would be feasible, making it a great board play with RTOS plus FoC motor control.

Even SimpleFoC could received the infrastructure to be seen as a Zephyr external module and runs on top of it.

If you don't oppose, I would like to port it to this project upstream.

Your thoughts @runger1101001 , @samuk , @jerinpeter , @sathya131295

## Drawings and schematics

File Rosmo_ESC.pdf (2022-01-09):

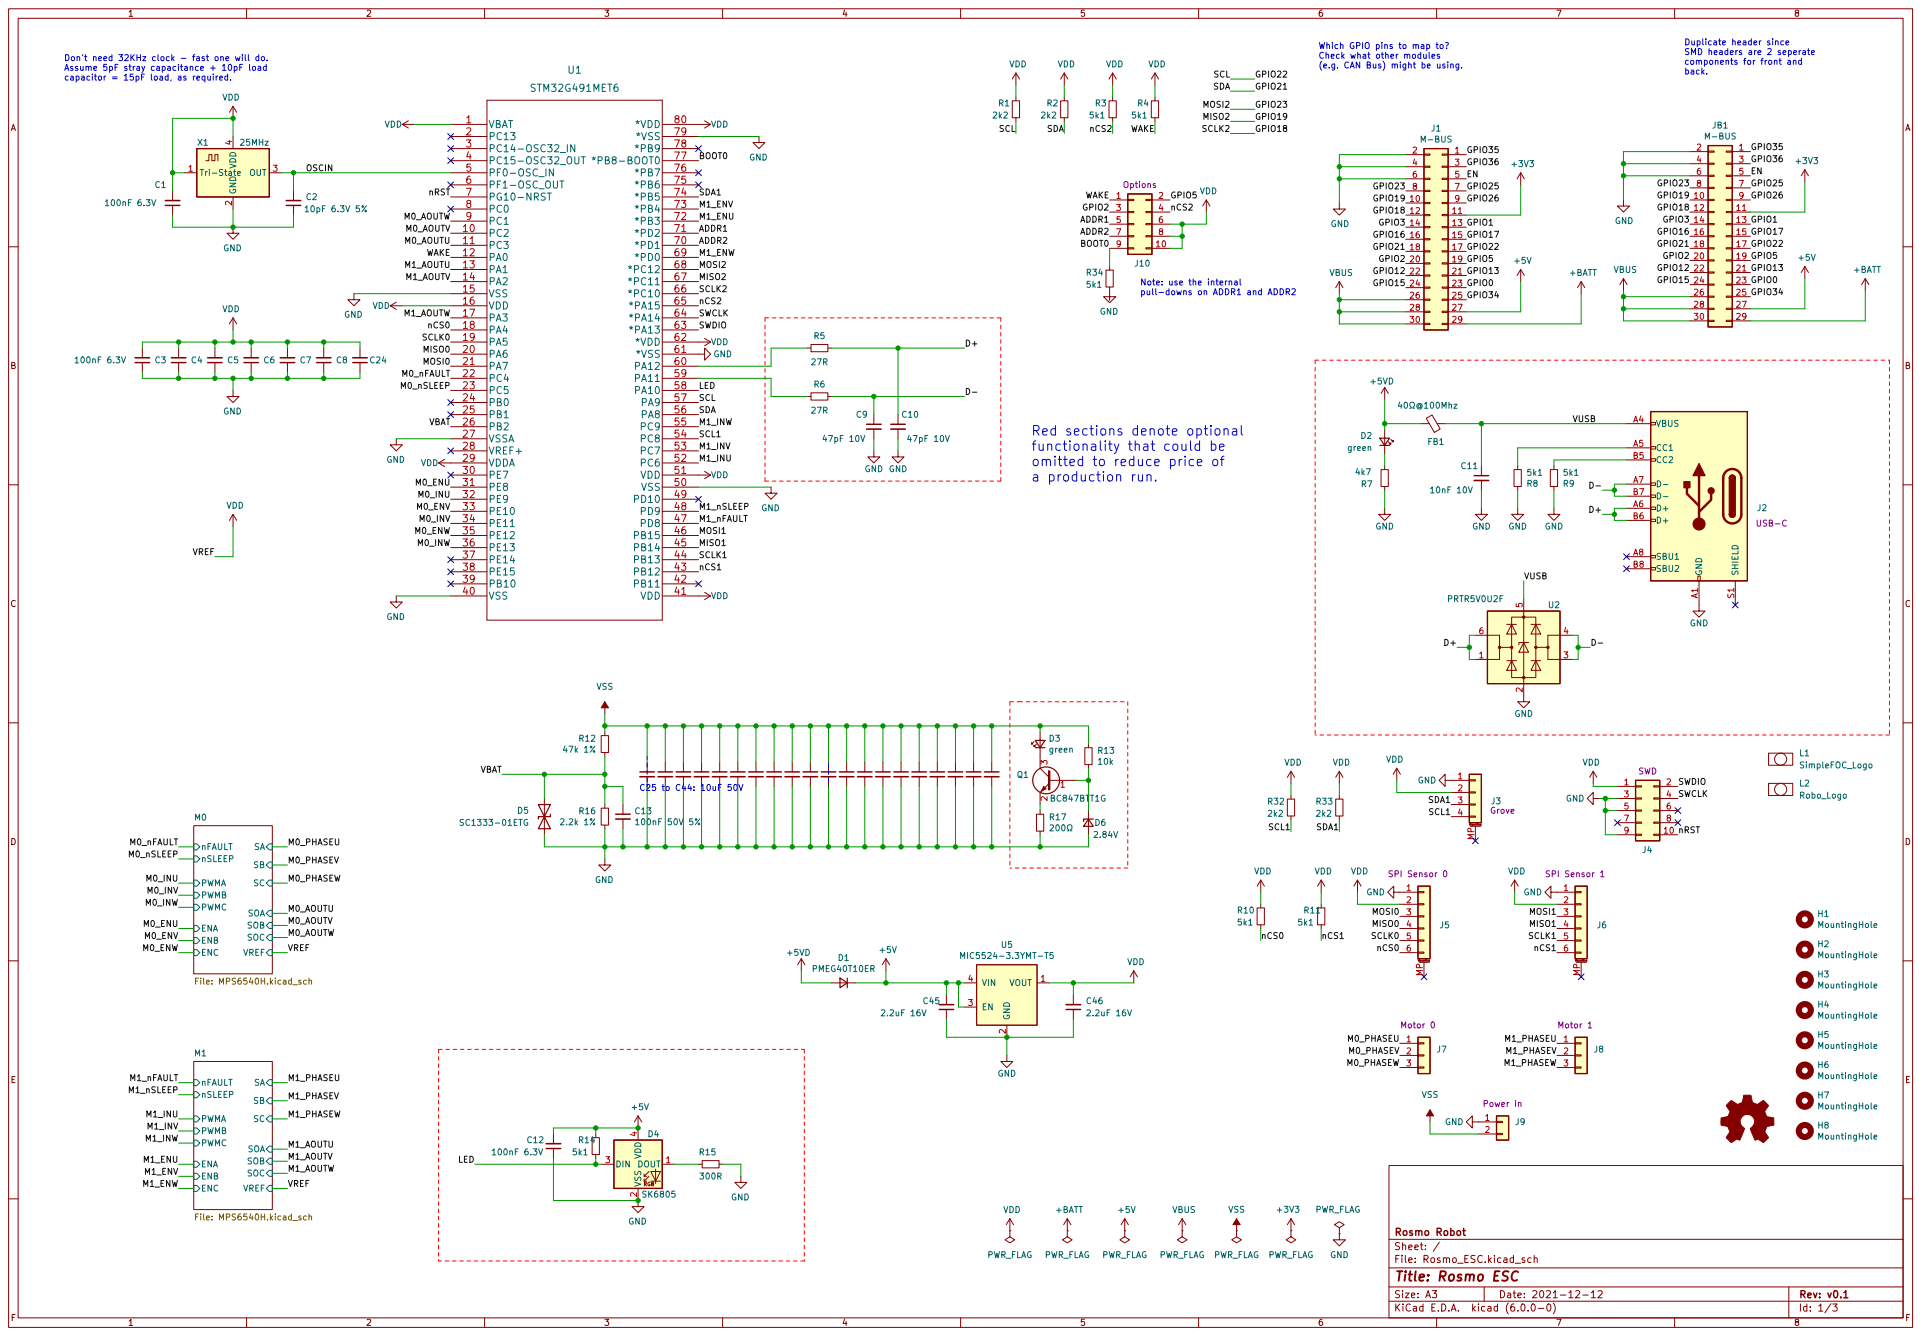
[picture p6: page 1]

Which GPIO pins to map to? Check what other modules (e.g. CAN Bus) might be using.

Duplicate header since
SMD headers are 2 seperate
components for front and

back. þÿDon t need 32KHz clock - fast one will do.
Assume 5pF stray capacitance + 10pF load
capacitor = 15pF load, as required.

functionality that could be
omitted to reduce price of
a production run.

PWMA
PWMB
File: Rosmo_ESC.kicad_sch Sheet: / Rosmo Robot PWMC

Id: 1/3 Title: Rosmo ESC

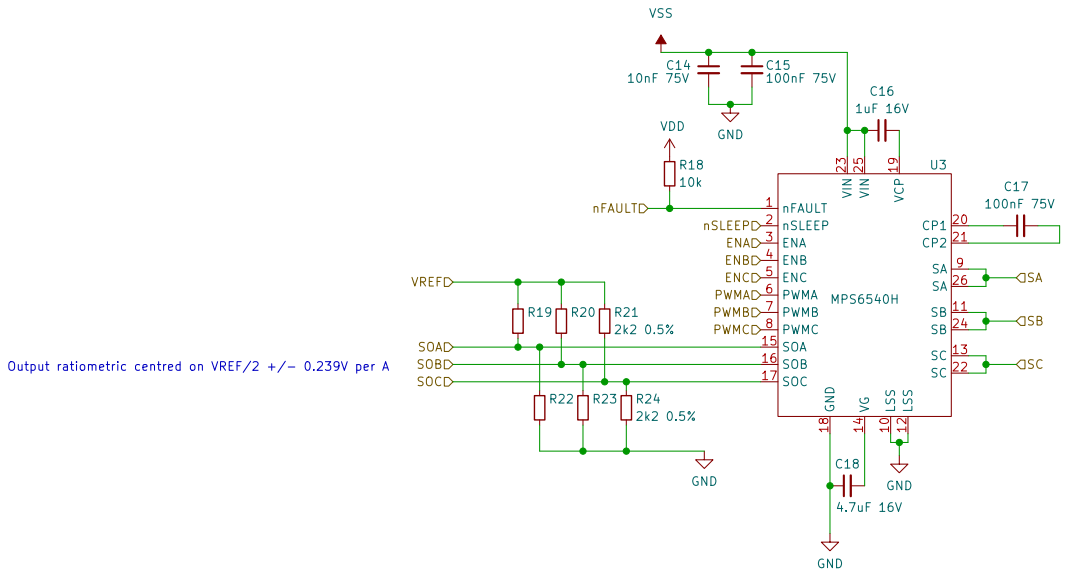
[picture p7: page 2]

SA Output ratiometric centred on VREF/2 +/- 0.239V per A

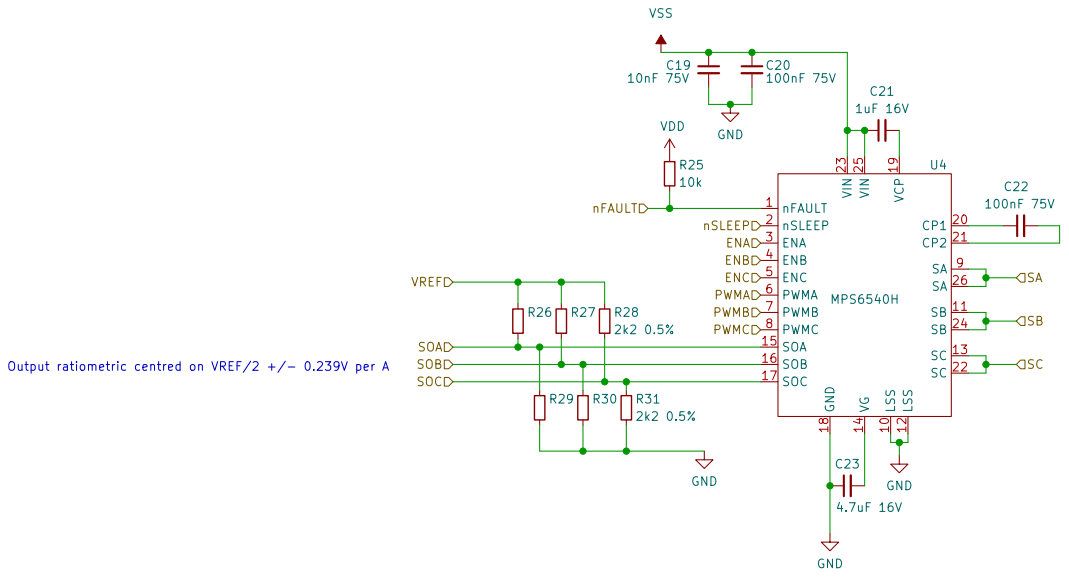
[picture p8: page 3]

SA Output ratiometric centred on VREF/2 +/- 0.239V per A

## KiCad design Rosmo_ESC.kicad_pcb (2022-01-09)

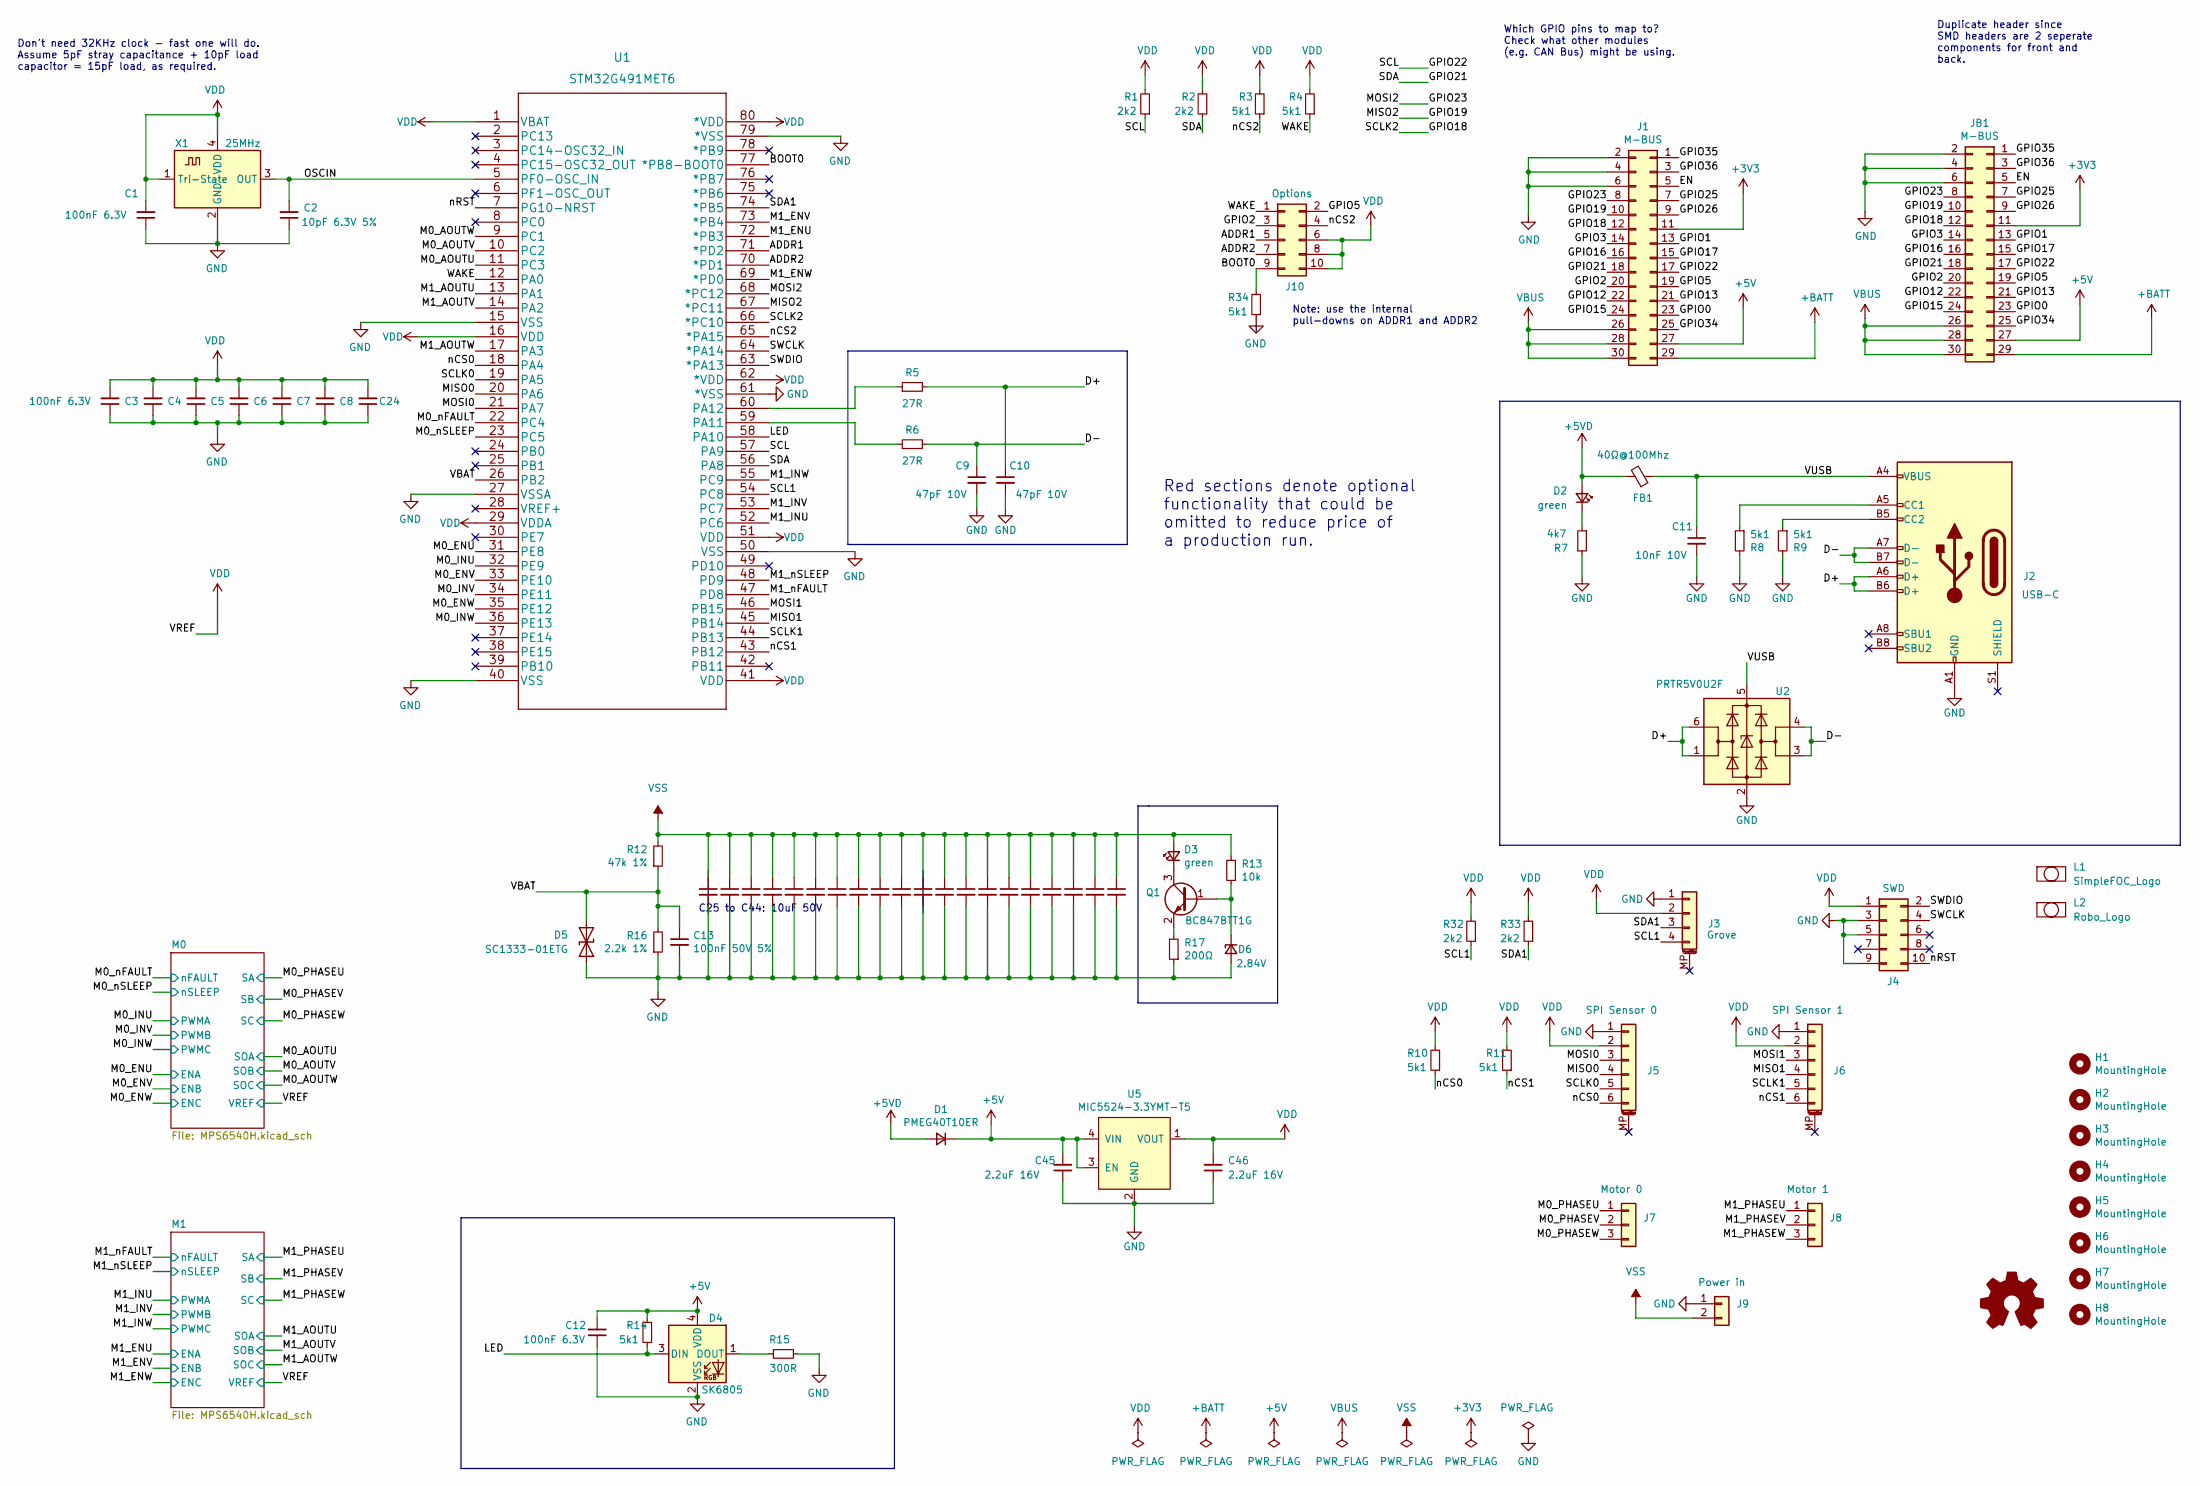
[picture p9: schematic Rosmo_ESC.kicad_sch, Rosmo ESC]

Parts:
C1, C3, C4, C5, C6, C7, C8, C12, C24: 100nF 6.3V; C_0402_1005Metric; Part CL05B104KQ5NNNC
C2: 10pF 6.3V 5%; C_0402_1005Metric; Part 04026A100JAT2A
C9, C10: 47pF 10V; C_0402_1005Metric; Part VJ0402A470GXQCW1BC
C11: 10nF 10V; C_0402_1005Metric; Part LMF105B7103KVHF
C13: 100nF 50V 5%; C_0402_1005Metric; Part GRM155C71H104JE19D
C25, C26, C27, C28, C29, C30, C31, C32, C33, C34, C35, C36, C37, C38, C39, C40, C41, C42, C43, C44: 10uF 50V; C_0805_2012Metric; Part GRM21BR61H106KE43L
C45, C46: 2.2uF 16V; C_0603_1608Metric; Part EMK107ABJ225KA8T
D1: PMEG40T10ER; D_SOD-123; Part PMEG40T10ER
D2, D3: green; LED_0402_1005Metric; Part 150040VS73240
D4: SK6805; LED_SK6805_PLCC4_2.4x2.7mm_P1.3mm; Part SK6805-2427
D5: SC1333-01ETG; D_0402_1005Metric; Part SC1333-01ETG
D6: 2.84V; D_SOD-523; Part CZRU52C2V7-HF
FB1: 40Ω@100Mhz; L_0805_2012Metric; Part MI0805K400R-10
H1, H2, H3, H4: MountingHole; BF@MountingHole_3.2mm_M3
H5, H6, H7, H8: MountingHole; BF@MountingHole_2.2mm_M2
J1: M-BUS; BF@M5Stack_MBUS; Part 89898-315BLF
J2: USB_C_Receptacle_USB2.0; USB_C_Receptacle_HRO_TYPE-C-31-M-12; Part HRO_TYPE-C-31-M-12
J3: Conn_01x04_MountingPin; Grove_A2006WF-04A; Part GR008WR-S-4P
J4, J10: Conn_02x05; PinHeader_2x05_P1.27mm_Vertical_SMD; Part 20021121-00010C8LF
J5, J6: JST_SH_SM06B-SRSS-TB_1x06-1MP; JST_SH_SM06B-SRSS-TB_1x06-1MP_P1.00mm_Horizontal; Part JST_SH_SM06B-SRSS-TB_1x06-1MP
J7, J8: Conn_01x03; TerminalBlock_Phoenix_PT-1,5-3-3.5-H_1x03_P3.50mm_Horizontal; Part 20020110-C034A01LF
J9: Conn_01x02; TerminalBlock_Phoenix_PT-1,5-2-3.5-H_1x02_P3.50mm_Horizontal; Part 20020110-C021A01LF
JB1: M-BUS; PinHeader_2x15_P2.54mm_Vertical_SMD; Part TSM-115-04-T-DV
L1: SimpleFOC_Logo; MadeForSimpleFOC_16mm
L2: Robo_Logo; Robo_logo2
L3: Logo_Open_Hardware_Small; OSHW-Symbol_6.7x6mm_SilkScreen
Q1: BC847BTT1G; SOT-416; Part BC847BTT1G
R1, R2, R32, R33: 2k2; R_0402_1005Metric
R3, R4, R8, R9, R10, R11, R14, R34: 5k1; R_0402_1005Metric
R5, R6: 27R; R_0402_1005Metric
R7: 4k7; R_0402_1005Metric
R12: 47k 1%; R_0402_1005Metric; Part CRCW040247K0FKEDC
R13: 10k; R_0402_1005Metric
R15: 300R; R_0402_1005Metric
R16: 2.2k 1%; R_0402_1005Metric; Part RT0402DRE072K2L
R17: 200Ω; R_0402_1005Metric
U1: STM32G491MET6; LQFP-80_12x12mm_P0.5mm; Part STM32G491MET6
U2: PRTR5V0U2F; SOT-886; Part PRTR5V0U2F
U5: MIC5524-3.3YMT-T5; TDFN-4-1EP_1x1mm_P0.65mm_EP0.5x0.5mm; Part MIC5524-3.3YMT-T5
X1: 25MHz; Oscillator_SMD_Abracon_ASCO-4Pin_1.6x1.2mm; Part ASCO-25.000MHZ-EK-T3

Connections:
+3V3: J1.11, JB1.11
+5V: C12.2, C45.2, D1.1 (K), D4.4 (VDD), J1.27, JB1.27, R14.2, U5.3 (EN), U5.4 (VIN)
+5VD: D1.2 (A), D2.2 (A), FB1.2
+BATT: J1.29, JB1.29
/ADDR1: J10.5, U1.71 (*PD2)
/ADDR2: J10.7, U1.70 (*PD1)
/BOOT0: J10.9, R34.2, U1.77 (*PB8-BOOT0)
/D+: C10.1, J2.A6 (D+), J2.B6 (D+), R5.2, U2.1 (I/O1), U2.6 (I/O1)
/D-: C9.1, J2.A7 (D-), J2.B7 (D-), R6.2, U2.3 (I/O2), U2.4 (I/O2)
/EN: J1.5, JB1.5
/GPIO0: J1.23, JB1.23
/GPIO1: J1.13, JB1.13
/GPIO2: J1.20, J10.3, JB1.20
/GPIO3: J1.14, JB1.14
/GPIO5: J1.19, J10.2, JB1.19
/GPIO12: J1.22, JB1.22
/GPIO13: J1.21, JB1.21
/GPIO15: J1.24, JB1.24
/GPIO16: J1.16, JB1.16
/GPIO17: J1.15, JB1.15
/GPIO18: J1.12, JB1.12, U1.66 (*PC10)
/GPIO19: J1.10, JB1.10, U1.67 (*PC11)
/GPIO21: J1.18, JB1.18, R2.1, U1.56 (PA8)
/GPIO22: J1.17, JB1.17, R1.1, U1.57 (PA9)
/GPIO23: J1.8, JB1.8, U1.68 (*PC12)
/GPIO25: J1.7, JB1.7
/GPIO26: J1.9, JB1.9
/GPIO34: J1.25, JB1.25
/GPIO35: J1.1, JB1.1
/GPIO36: J1.3, JB1.3
/LED: D4.3 (DIN), R14.1, U1.58 (PA10)
/M0_AOUTU: U1.11 (PC3); also elsewhere on the board
/M0_AOUTV: U1.10 (PC2); also elsewhere on the board
/M0_AOUTW: U1.9 (PC1); also elsewhere on the board
/M0_ENU: U1.31 (PE8); also elsewhere on the board
/M0_ENV: U1.33 (PE10); also elsewhere on the board
/M0_ENW: U1.35 (PE12); also elsewhere on the board
/M0_INU: U1.32 (PE9); also elsewhere on the board
/M0_INV: U1.34 (PE11); also elsewhere on the board
/M0_INW: U1.36 (PE13); also elsewhere on the board
/M0_PHASEU: J7.1; also elsewhere on the board
/M0_PHASEV: J7.2; also elsewhere on the board
/M0_PHASEW: J7.3; also elsewhere on the board
/M0_nFAULT: U1.22 (PC4); also elsewhere on the board
/M0_nSLEEP: U1.23 (PC5); also elsewhere on the board
/M1_AOUTU: U1.13 (PA1); also elsewhere on the board
/M1_AOUTV: U1.14 (PA2); also elsewhere on the board
/M1_AOUTW: U1.17 (PA3); also elsewhere on the board
/M1_ENU: U1.72 (*PB3); also elsewhere on the board
/M1_ENV: U1.73 (*PB4); also elsewhere on the board
/M1_ENW: U1.69 (*PD0); also elsewhere on the board
/M1_INU: U1.52 (PC6); also elsewhere on the board
/M1_INV: U1.53 (PC7); also elsewhere on the board
/M1_INW: U1.55 (PC9); also elsewhere on the board
/M1_PHASEU: J8.1; also elsewhere on the board
/M1_PHASEV: J8.2; also elsewhere on the board
/M1_PHASEW: J8.3; also elsewhere on the board
/M1_nFAULT: U1.47 (PD8); also elsewhere on the board
/M1_nSLEEP: U1.48 (PD9); also elsewhere on the board
/MISO0: J5.4, U1.20 (PA6)
/MISO1: J6.4, U1.45 (PB14)
/MOSI0: J5.3, U1.21 (PA7)
/MOSI1: J6.3, U1.46 (PB15)
/OSCIN: C2.2, U1.5 (PF0-OSC_IN), X1.3 (OUT)
/SCL1: J3.4, R32.1, U1.54 (PC8)
/SCLK0: J5.5, U1.19 (PA5)
/SCLK1: J6.5, U1.44 (PB13)
/SDA1: J3.3, R33.1, U1.74 (*PB5)
/SWCLK: J4.4, U1.64 (*PA14)
/SWDIO: J4.2, U1.63 (*PA13)
/VBAT: C13.1, D5.2 (A2), R12.1, R16.2, U1.26 (PB2)
/VUSB: C11.1, FB1.1, J2.A4 (VBUS), J2.A9 (VBUS), J2.B4 (VBUS), J2.B9 (VBUS), U2.5 (VBUS)
/WAKE: J10.1, R4.1, U1.12 (PA0)
/nCS0: J5.6, R10.1, U1.18 (PA4)
/nCS1: J6.6, R11.1, U1.43 (PB12)
/nCS2: J10.4, R3.1, U1.65 (*PA15)
/nRST: J4.10, U1.7 (PG10-NRST)
GND: C1.1, C2.1, C3.1, C4.1, C5.1, C6.1, C7.1, C8.1, C9.2, C10.2, C11.2, C12.1, C13.2, C24.1, C25.2, C26.2, C27.2, C28.2, C29.2, C30.2, C31.2, C32.2, C33.2, C34.2, C35.2, C36.2, C37.2, C38.2, C39.2, C40.2, C41.2, C42.2, C43.2, C44.2, C45.1, C46.1, D4.2 (VSS), D5.1 (A1), D6.2 (A), J1.2, J1.4, J1.6, J2.A1 (GND), J2.A12 (GND), J2.B1 (GND), J2.B12 (GND), J3.1, J4.3, J4.5, J4.9, J5.1, J6.1, J9.1, JB1.2, JB1.4, JB1.6, R7.2, R8.2, R9.2, R15.1, R16.1, R17.1, R34.1, U1.15 (VSS), U1.27 (VSSA), U1.40 (VSS), U1.50 (VSS), U1.61 (*VSS), U1.79 (*VSS), U2.2 (GND), U5.2 (GND), U5.5 (GND), X1.2 (GND); also elsewhere on the board
unnamed: D2.1 (K), R7.1
unnamed: D3.1 (K), Q1.3 (C)
unnamed: D4.1 (DOUT), R15.2
unnamed: D6.1 (K), Q1.1 (B), R13.1
unnamed: J2.A5 (CC1), R8.1
unnamed: J2.B5 (CC2), R9.1
unnamed: Q1.2 (E), R17.2
unnamed: R5.1, U1.60 (PA12)
unnamed: R6.1, U1.59 (PA11)
VBUS: J1.26, J1.28, J1.30, JB1.26, JB1.28, JB1.30
VDD: C1.2, C3.2, C4.2, C5.2, C6.2, C7.2, C8.2, C24.2, C46.2, J3.2, J4.1, J5.2, J6.2, J10.6, J10.8, J10.10, R1.2, R2.2, R3.2, R4.2, R10.2, R11.2, R32.2, R33.2, U1.1 (VBAT), U1.16 (VDD), U1.29 (VDDA), U1.41 (VDD), U1.51 (VDD), U1.62 (*VDD), U1.80 (*VDD), U5.1 (VOUT), X1.1 (Tri-State), X1.4 (VDD); also elsewhere on the board
VSS: C25.1, C26.1, C27.1, C28.1, C29.1, C30.1, C31.1, C32.1, C33.1, C34.1, C35.1, C36.1, C37.1, C38.1, C39.1, C40.1, C41.1, C42.1, C43.1, C44.1, D3.2 (A), J9.2, R12.2, R13.2; also elsewhere on the board

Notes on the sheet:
Which GPIO pins to map to? Check what other modules (e.g. CAN Bus) might be using.
C25 to C44: 10uF 50V
Don’t need 32KHz clock - fast one will do. Assume 5pF stray capacitance + 10pF load capacitor = 15pF load, as required.
Duplicate header since SMD headers are 2 seperate components for front and back.
Red sections denote optional functionality that could be omitted to reduce price of a production run.
Note: use the internal pull-downs on ADDR1 and ADDR2

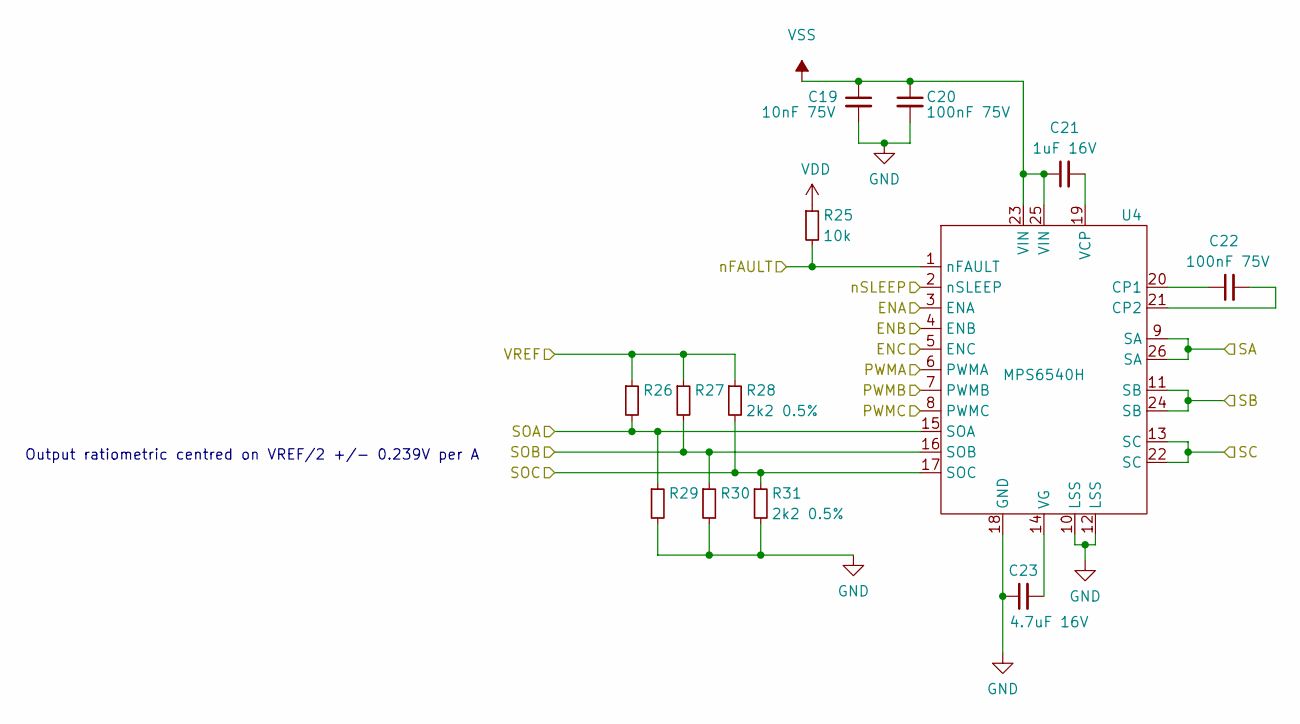
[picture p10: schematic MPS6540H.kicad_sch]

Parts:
C19: 10nF 75V; C_0805_2012Metric; Part GRM21BR72A103KA01K
C20, C22: 100nF 75V; C_0805_2012Metric; Part GCM21BR72A104KA37L
C21: 1uF 16V; C_0603_1608Metric; Part GCM188R71C105KA64J
C23: 4.7uF 16V; C_0603_1608Metric; Part GRT188C71C475KE13D
R25: 10k; R_0402_1005Metric
R26, R27, R28, R29, R30, R31: 2k2 0.5%; R_0402_1005Metric; Part RT0402DRE072K2L
U4: MPS6540H; Part MPS6540H

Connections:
/M1_AOUTU: R26.2, R29.1, U4.15 (SOA); also elsewhere on the board
/M1_AOUTV: R27.2, R30.1, U4.16 (SOB); also elsewhere on the board
/M1_AOUTW: R28.2, R31.1, U4.17 (SOC); also elsewhere on the board
/M1_ENU: U4.3 (ENA); also elsewhere on the board
/M1_ENV: U4.4 (ENB); also elsewhere on the board
/M1_ENW: U4.5 (ENC); also elsewhere on the board
/M1_INU: U4.6 (PWMA); also elsewhere on the board
/M1_INV: U4.7 (PWMB); also elsewhere on the board
/M1_INW: U4.8 (PWMC); also elsewhere on the board
/M1_PHASEU: U4.9 (SA), U4.26 (SA); also elsewhere on the board
/M1_PHASEV: U4.11 (SB), U4.24 (SB); also elsewhere on the board
/M1_PHASEW: U4.13 (SC), U4.22 (SC); also elsewhere on the board
/M1_nFAULT: R25.2, U4.1 (nFAULT); also elsewhere on the board
/M1_nSLEEP: U4.2 (nSLEEP); also elsewhere on the board
GND: C19.2, C20.2, C23.1, R29.2, R30.2, R31.2, U4.10 (LSS), U4.12 (LSS), U4.18 (GND); also elsewhere on the board
unnamed: C21.2, U4.19 (VCP)
unnamed: C22.1, U4.20 (CP1)
unnamed: C22.2, U4.21 (CP2)
unnamed: C23.2, U4.14 (VG)
VDD: R25.1, R26.1, R27.1, R28.1; also elsewhere on the board
VSS: C19.1, C20.1, C21.1, U4.23 (VIN), U4.25 (VIN); also elsewhere on the board

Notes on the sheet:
Output ratiometric centred on VREF/2 +/- 0.239V per A

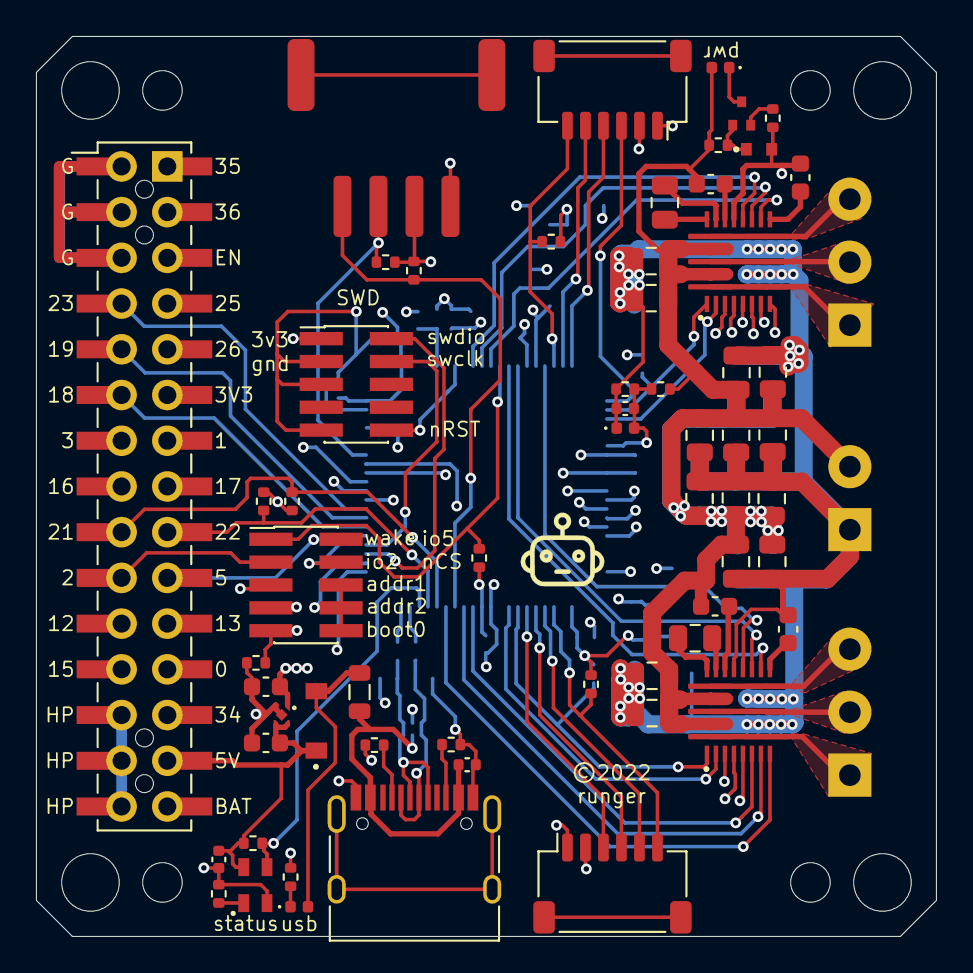
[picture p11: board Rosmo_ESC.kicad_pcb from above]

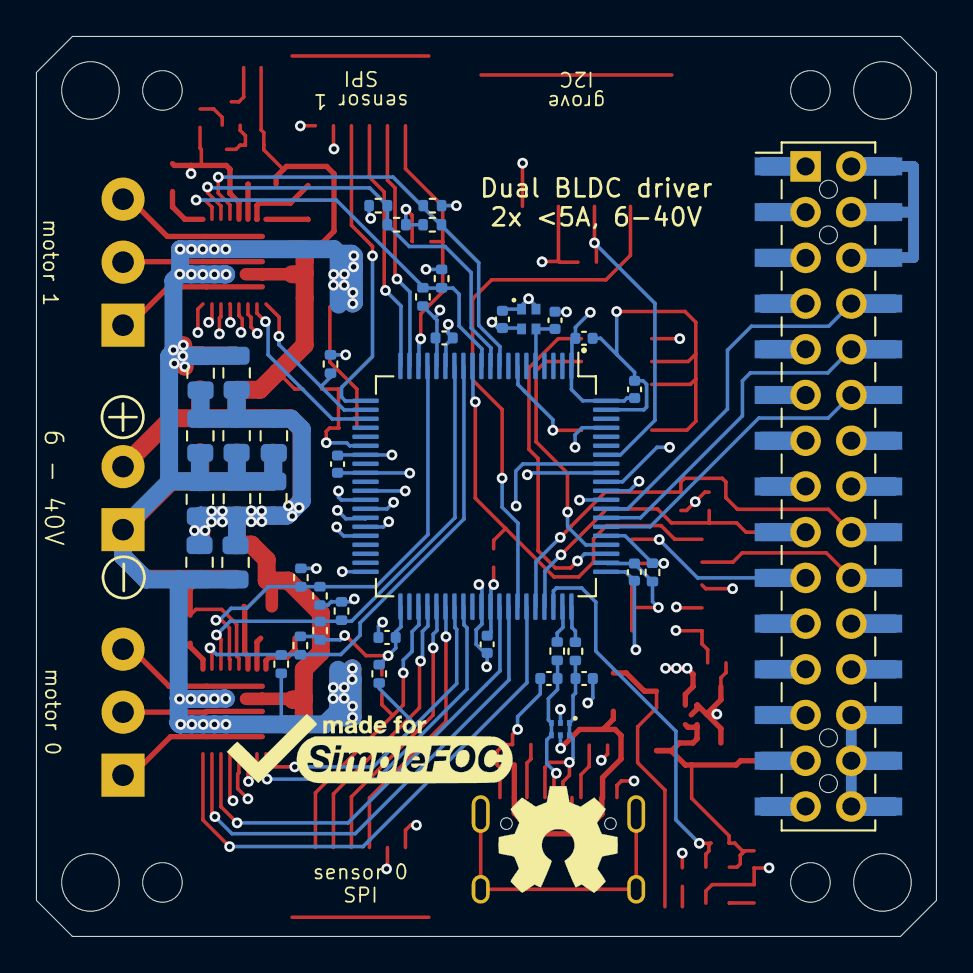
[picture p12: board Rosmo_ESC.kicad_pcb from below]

Board: 4 copper layers, 50.0 x 50.0 mm, 116 parts (44 on the bottom side), 98 nets.

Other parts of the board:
C14: 10nF 75V; C_0805_2012Metric
C15, C17: 100nF 75V; C_0805_2012Metric
C16: 1uF 16V; C_0603_1608Metric
C18: 4.7uF 16V; C_0603_1608Metric
R18: 10k; R_0402_1005Metric
R19, R20, R21, R22, R23, R24: 2k2 0.5%; R_0402_1005Metric
U3: MPS6540H

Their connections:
/M0_AOUTU: R19.2, R22.1, U3.15 (SOA); also elsewhere on the board
/M0_AOUTV: R20.2, R23.1, U3.16 (SOB); also elsewhere on the board
/M0_AOUTW: R21.2, R24.1, U3.17 (SOC); also elsewhere on the board
/M0_ENU: U3.3 (ENA); also elsewhere on the board
/M0_ENV: U3.4 (ENB); also elsewhere on the board
/M0_ENW: U3.5 (ENC); also elsewhere on the board
/M0_INU: U3.6 (PWMA); also elsewhere on the board
/M0_INV: U3.7 (PWMB); also elsewhere on the board
/M0_INW: U3.8 (PWMC); also elsewhere on the board
/M0_PHASEU: U3.9 (SA), U3.26 (SA); also elsewhere on the board
/M0_PHASEV: U3.11 (SB), U3.24 (SB); also elsewhere on the board
/M0_PHASEW: U3.13 (SC), U3.22 (SC); also elsewhere on the board
/M0_nFAULT: R18.2, U3.1 (nFAULT); also elsewhere on the board
/M0_nSLEEP: U3.2 (nSLEEP); also elsewhere on the board
GND: C14.2, C15.2, C18.1, R22.2, R23.2, R24.2, U3.10 (LSS), U3.12 (LSS), U3.18 (GND); also elsewhere on the board
unnamed: C16.2, U3.19 (VCP)
unnamed: C17.1, U3.20 (CP1)
unnamed: C17.2, U3.21 (CP2)
unnamed: C18.2, U3.14 (VG)
VDD: R18.1, R19.1, R20.1, R21.1; also elsewhere on the board
VSS: C14.1, C15.1, C16.1, U3.23 (VIN), U3.25 (VIN); also elsewhere on the board

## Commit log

2021-11-29 first commit, unfinished, just looking at dimensions
    [MPS6540H.kicad_sch, Rosmo_ESC.kicad_pcb, Rosmo_ESC.kicad_sch]
2021-12-14 working on rosmo ESC, routing half done
    [MPS6540H.kicad_sch, Rosmo_ESC.kicad_pcb, Rosmo_ESC.kicad_sch]
2021-12-14 updated README, added schematic PDF
    [Rosmo_ESC.kicad_sch]
2021-12-17 intial routing done
    [MPS6540H.kicad_sch, Rosmo_ESC.kicad_pcb, Rosmo_ESC.kicad_sch]
2022-01-03 updated to KiCad 6
    [MPS6540H.kicad_sch, Rosmo_ESC.kicad_pcb, Rosmo_ESC.kicad_sch]
2022-01-04 refer to KiCad 6 in README.
2022-01-09 v1 prototype for production
    [MPS6540H.kicad_sch, Rosmo_ESC.kicad_pcb, Rosmo_ESC.kicad_sch]
2022-01-10 updated pinout diagramme
    [Rosmo_ESC.kicad_sch]

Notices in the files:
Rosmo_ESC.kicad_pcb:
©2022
